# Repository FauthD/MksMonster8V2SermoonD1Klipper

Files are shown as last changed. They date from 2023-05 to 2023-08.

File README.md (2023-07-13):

# MksMonster8V2SermoonD1Klipper
Klipper settings for MKS Monster8 V2 build into the Creality Sermoon D1

This is WIP, do not use it yet.
I will add details here when it is ready and works.

# CAUTION: DO not use DFU with 24V connected with this board.
It can kill transistor Q7 (turning on bed heater all the time and Q7 gets very hot).
See there

[Bed is always heated after upgrade FW to v0.11.0-241-gffb5105b](https://github.com/makerbase-mks/MKS-Monster8/issues/40)

and

[V2 board starts burning when attempting dfu mode](https://github.com/makerbase-mks/MKS-Monster8/issues/26)

# Progress
[You can see many installation details there](InstallationJournal.md).

## Mechanics
Created an adapter to mount the Monster8 since it does not fit to the mounting holes. I also added some mounts for a big 120mm fan (because it was easier with a fan larger than the board). The fan runs with about 600 rmp and is barly audible.
There are also 3 mounting places for typical Step-Down regulators. I only use two for the fans, the third is spare.

Note: The monster board has 12V outputs for fans, so I would only need one step-down for the mainboard fan (7V), but the 12V step down was already wired from hystory (SKR 3 board). I am too lazy to change that right now.

| With 120mm fan |
| :----: |
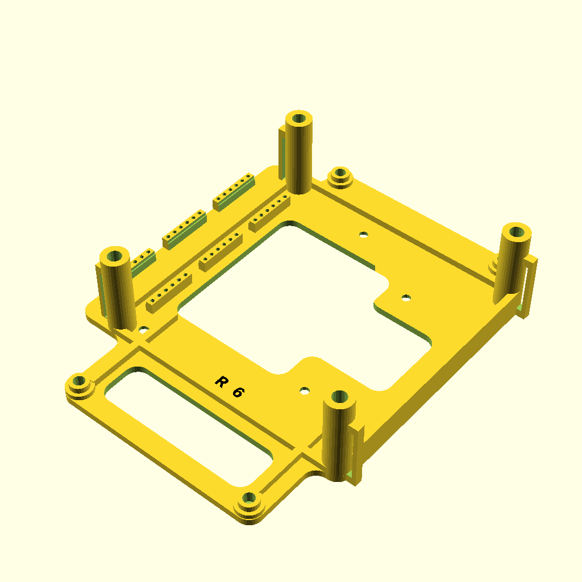
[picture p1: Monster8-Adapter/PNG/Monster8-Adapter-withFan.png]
|  

Note: You either need to cut a hole onto the bottom sheet or replace it with some new and larger feet (my plan).

Note2: The original mainboard fan does not transport much air, but makes quite some noise. So a slow turning 120mm fan is much better.
The next source of noise is the fan in the power supply. I replaced that fan with a low noise 120mm fan. Now it is barly audible.

Note3: We need heigher feet. Already printed some test feet with 28mm height (need 40mm screws - probably will increase by 5mm when I have that screws available).

Note4: I cannot check whether the original wires are long enough since I did buy the printer used and the wires are not original anymore.
## Klipper

Working on this.

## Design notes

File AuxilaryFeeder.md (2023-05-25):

# Auxilary feeder
## Rational
You might wonder why I do this? With my Sermoon D1 I often had issues with under extrution or the start of the print failed because the filament slipped out of the feeder. The first issue probably reulted ifrom the way I store the filament.

The extra feeder shall avoid transport problems.

## Hardware connection
The Monster 8 has 8 stepper drivers. For this auxilary feeder I use the driver5:E2.

This is the portion of the .cfg file. It is loctaed inside the extruder.cfg

```
[extruder_stepper auxilary_feeder]
extruder: extruder
# The extruder this stepper is synchronized to. If this is set to an
#  empty string then the stepper will not be synchronized to an
#  extruder. This parameter must be provided.
step_pin: PD2
dir_pin: PD1
enable_pin: !PD3
microsteps: 16
rotation_distance: 32.83
# See the "stepper" section for the definition of the above
# parameters.

[tmc2209 extruder_stepper auxilary_feeder]
uart_pin: PD0
run_current: 0.600
diag_pin:
```

## Testing low level
As with other steppers you can move the stepper back and forth with that command:

`STEPPER_BUZZ STEPPER="extruder_stepper auxilary_feeder"`

At my very first try it did not work, the enable pin needs the inverion flag: 
`enable_pin: !PD3`. After that the Stepper moved back and forth 10 times. (actually forth and back).

## Testing syncronization with extruder
Both the extruder (feeder) and the auxilary_feeder need to tranport the filament in sync. Therefor it should be sufficient to start extruding and the auxilary_feeder should transport the same ammount of filament. At this stage the amounts could still differ if the wheels have different diameters or the steps/mm are not the same.

So at least I want to see some transport.
1. Heat up the hotend to 200°C
2. Wait for heating up
3. Have filament in both the regular extruder and the auxilary one.
	I had used different filament pieces so they are independent from each other at this stage.
4. In the dashboard click on extrude.
5. Filamanets in both extruders should move in the same direction.
6. Same with retract.

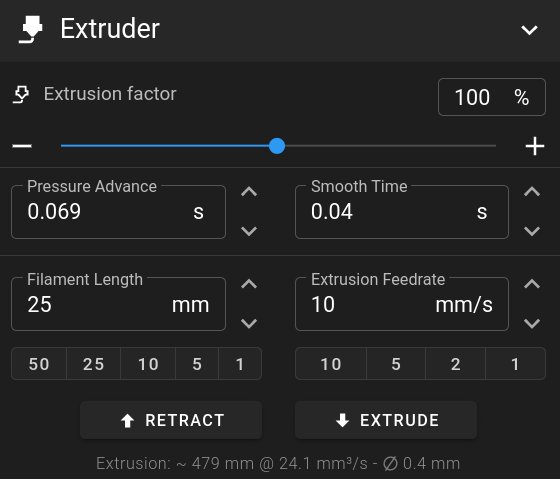
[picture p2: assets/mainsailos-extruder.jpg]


## Testing the amount of filament
Both extruders must transport the exact same amount of filament. For the test I use PLA from same manufacturer.

1. Mark the filamant in both feeders in same way as described in the Klipper docs (70mm).
	https://www.klipper3d.org/Rotation_Distance.html.
2. Set to relative coordinates `G91`.
3. Extrude 50mm with a slow speed `G1 E50 F60` to reduce the impact of filament melting.
4. Measure the (formerly) 70mm marks. They now should be 20mm away from the reference point.
	If not, calculate new rotation_distance values as described in the Klipper docs.
	In my case it was 20mm for both strings.
5. Do the same test with a higher speed `G1 E50 F600`.
	In my case there was quite a difference. Auxilary feeder was still at 20mm, but the normal feeder/extruder was at 35mm that means it only feeds 35mm instead 50mm.
	Currently I do not understand why the difference is that big.

# Reserching different filamant transport
Since the last test was not too pleasing, I tried the same with a heigher temperature (225 vs 200).
This time the normal extruder was at 32mm. A bit more filament was feed, but still way too less.

This could be a sign that my extruder has an issue. Or my expectations are plain wrong. Most likely the latter.

Increasing the current from 0.6A to 0.8A did not change much. I had hoped we loose steps, though normally this could be heared.

With `G1 E50 F200` the rest was 23mm which is still 3mm to less.

Visually I see the speed of the filament changes a bit while the test runs.
I will check the brass wheel of the extruder, but need to take it appart for this. What I can so so far it does not look too bad, but also not perfect. The allen screw sits absolut locked, need to take the complete head appart for better handling.

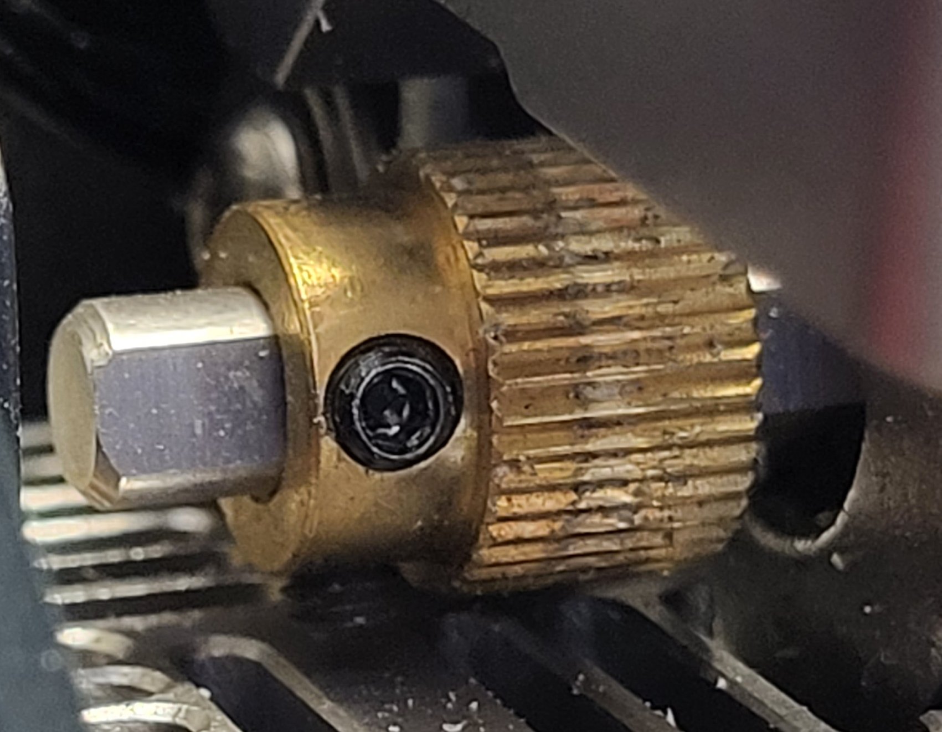
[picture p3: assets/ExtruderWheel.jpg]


With a new wheel it seems better, but at `G1 E50 F600` the extruder klicks. It is a sign that the old wheel was worn out.
Still a lot to do here. I guess it has nothing to do with the auxilary feeder, was just found randomly.

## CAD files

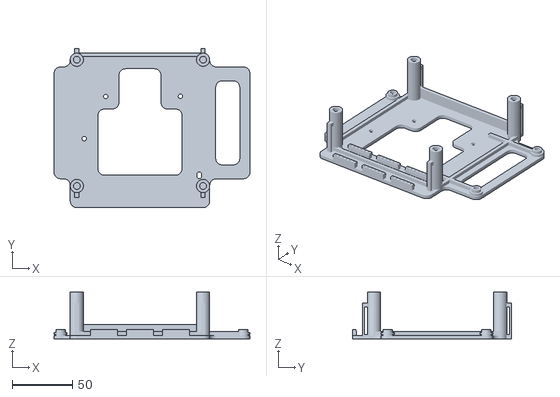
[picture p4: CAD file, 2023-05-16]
Monster8-Adapter/STL/Monster8-Adapter-withFan.stl
163.0 x 132.6 x 39.0

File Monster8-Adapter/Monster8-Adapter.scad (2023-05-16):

// An adapter to mount the MKS Monster 8 board into Creality mounting holes.
// Aimed for the Sermoon D1.
// For mounting you need 4 * M3 heat inserts (OD=5mm, l=4mm).
// I recommend to replace the original screws from the old board with ones with 
// flatter head.
// For the Fan you need 4 * M4 heat inserts (OD=6mm, l=5mm).
// Copyright (C) 2023 Dieter Fauth
// This program is free software: you can redistribute it and/or modify it under the terms of the GNU General Public License as published by the Free Software Foundation, either version 3 of the License, or (at your option) any later version.
// This program is distributed in the hope that it will be useful, but WITHOUT ANY WARRANTY; without even the implied warranty of MERCHANTABILITY or FITNESS FOR A PARTICULAR PURPOSE. See the GNU General Public License for more details. You should have received a copy of the GNU General Public License along with this program. If not, see <http://www.gnu.org/licenses/>.
// Contact: dieter.fauth at web.de

/* [Print] */

PrintThis = "all"; // ["all", "mount", "nothing"]

/* [Board Sizes] */
BoardLenght=160;
BoardWidth=90;

DrillLenght=152;
DrillWidth=82;
CrealityDrillDiameter=3.8;
// For M3 heat inserts use 4.5 else 2.5.
BoardDrillDiameter=4.7;
MountDiameter=8;
MountDiameter2=11;

MountHeight=6;
Thickness=3;

// Move Board to the left
Offset_X=-15;
// Move Board to upper
Offset_Y=10;

/* [Options] */
UseFan=true;
FanDiameter=120;
FanScrewDistance=105;
// For M4 heat inserts use 5.7 else 3.5.
FanScrewDiameters=5.7;
FanMountingPostDiameter=11;
FanHeight=36;
// Move Fan to the left
FanOffset_X=-10;

Fontsize=5;

/* [Hidden] */

module __Customizer_Limit__ () {}
    shown_by_customizer = false;

$fa = $preview ? 2 : 0.5;
$fs = $preview ? 1 : 0.5;

// If you enable the next line, the $fa and $fs are ignored.
// $fn = $preview ? 12 : 100;
Epsilon = 0.01;
epsilon = Epsilon;

include <svn_rev.scad>

/* Creality holes */
// These are relative to the lower left corner of the board.
// I took them from the BTT E3 Mini board.
// https://github.com/bigtreetech/BIGTREETECH-SKR-mini-E3/blob/master/hardware/BTT%20SKR%20MINI%20E3%20V3.0.1/Hardware/BTT%20E3%20SKR%20MINI%20V3.0.1_SIZE.pdf

E3Mini=[103.75, 70.25];

UnkownDifference=-1.0;  // one hole was not correct, empiric fix with a slotted hole

Drill1=[23.4,67.03, 0];
Drill2=[85.55, E3Mini.y-3.02, 0];
Drill3=[5.54, 32.05, 0];
Drill4=[37.34, 29.41, 0];
Drill5=[101.22, 2.56, 0];

Rounding=MountDiameter2/2;

FanOffset_Y=0;
Enlarge=3;

FanSize=FanScrewDistance+FanMountingPostDiameter;


///////////////////////////////////////////////////////////////////////////////
// halign: String. The horizontal alignment for the text. Possible values are "left", "center" and "right". Default is "left".
// valign : String. The vertical alignment for the text. Possible values are "top", "center", "baseline" and "bottom". Default is "baseline".

module WriteRevision(rev="", height=0.3, fontsize=6, font = "Liberation Mono:bold", halign="left", valign="top", mirror=false, rot=[0,0,0])
{
	rotate(rot)
		mirror([mirror?1:0,0,0])
			linear_extrude(height = height, center = true, convexity = 10)
			{
				text(rev, size=fontsize, font = font, halign=halign, valign=valign);
			}
}

///////////////////////////////////////////////////////////////////////////////
// Some helpers to round combined objects
module RoundConvex(r)
{
	offset(r = r)
	{
		offset(delta = -r)
		{
			children();
		}
	}
}

module RoundConcave(r)
{
	offset(r = -r)
	{
		offset(delta = r)
		{
			children();
		}
	}
}

module RoundThis(r)
{
	RoundConcave(r) RoundConvex(r) children();
}

// Can round combined 2D objects and make them 3D
module RoundExtrude(r, h)
{
	linear_extrude(height = h)
		RoundThis(r) children();
}

///////////////////////////////////////////////////////////////////////////////
// long hole
module SlottedHole(d, h, length)
{
   translate([0, 0, h/2])
      cube(size=[length, d, h+Epsilon], center=true);
      
   for(x=[-length/2,length/2])
   {
      translate([x, 0, h/2])
      {
         cylinder(d=d, h=h+Epsilon, center=true);
      }
   }
}

///////////////////////////////////////////////////////////////////////////////
// Helper for mounting step down boards with MP1584EN

module PcbMount(size, pcb)
{
   len=size.x;
   width=size.y+6;
   screw_dia=1.8;

   difference()
   {
      translate([0,0,size.z/2])
         cube([len,width, size.z], center=true);

      translate([0,0,size.z])
         cube([len+Epsilon,size.y, 2*pcb], center=true);

      translate([0,0,size.z/2])
         cube([len+Epsilon,size.y-1, size.z+Epsilon], center=true);

      for(n=[-1,1])
      {
         for(m=[-1:0.4:1])
         {
            translate([m*(len/2-2),n*(width/2-1.5),size.z/2])
               cylinder(d=screw_dia, h=20*size.z, center=true);
         }
      }
   }
}

MP1584EN_Size=[22.5, 17.1, 6.5];

module StepDown_MP1584EN()
{
   PcbMount(size=MP1584EN_Size, pcb=1.4);
}

///////////////////////////////////////////////////////////////////////////////
// The Fan

module Fan(h=25)
{
   for(a=[45:90:360-Epsilon])
   {
      rotate([0,0,a])
         translate([FanScrewDistance/1.414, 0, 0])
         {
            difference()
            {
               cylinder(d=FanMountingPostDiameter, h=h, center=true);
               translate([0,0,h/2])
                  cylinder(d=FanScrewDiameters, h=h, center=true);
            }
         }
   }
}
///////////////////////////////////////////////////////////////////////////////
// holder for cable tie
module CableMount(len=15, h=5)
{
	thick=3.5;
	translate([0,0,h/2])
		difference()
		{
			cube(size=[len, thick, h], center=true);

			translate([0,0,-thick/2])
				cube(size=[len-2*thick, 2*thick, h], center=true);
		}
}

///////////////////////////////////////////////////////////////////////////////
// The adapter

module CrealityHoles(d, h=5*Thickness)
{
   translate(Drill1)
      cylinder(d=d, h=h, center=true);
   translate(Drill2)
      cylinder(d=d, h=h, center=true);
   translate(Drill3)
      cylinder(d=d, h=h, center=true);
   translate(Drill4)
      cylinder(d=d, h=h, center=true);
   translate(Drill5)
      cylinder(d=d, h=h, center=true);
// fix some unknown difference in hole position
   translate([0,UnkownDifference,-h/2])
      translate(Drill5)
         rotate([0,0,90])
            SlottedHole(d=d, h=h, length=d/2);
}

module BoardHoles()
{
      for(x=[-1,1])
      {
         for(y=[-1,1])
         {
            translate([x*DrillLenght/2, y*DrillWidth/2, 0])
               cylinder(d=BoardDrillDiameter, h=10*Thickness);
         }
      }
}

module BasePlate()
{
   r=Rounding;

   RoundExtrude(r, Thickness)
   {
      square([BoardLenght+Enlarge, BoardWidth+Enlarge], center=true);
      // ensure the holes are covered by the size of the old board
      translate([Offset_X, -Offset_Y])
         square(E3Mini, center=true);


      x=E3Mini.x;
      y=E3Mini.y+7;
      translate([FanOffset_X, -12.5])
         square([FanSize, FanSize], center=true);

      if(UseFan)
      {
         translate([FanOffset_X, FanOffset_Y])
            square([FanSize, FanSize], center=true);
      }
   }
}

// also saves material
module CoolingHelper()
{
   RoundExtrude(Rounding, 10*Thickness)
   {
      translate([FanOffset_X+10, 15])
         square([35,60], center=true);

      translate([FanOffset_X+10, 25-DrillWidth/2])
         square([70,55], center=true);

      translate([BoardLenght/2-7, 0])
         square([20,70], center=true);
   }
}

module BoardMounts(l,w)
   {
      for(x=[-1,1])
      {
         for(y=[-1,1])
         {
            translate([x*l/2, y*w/2, MountHeight/2+Thickness])
               cylinder(d=MountDiameter, h=MountHeight, center=true);
            translate([x*l/2, y*w/2, MountHeight/2+Thickness-1])
               cylinder(d=MountDiameter2, h=MountHeight-3, center=true);
         }
      }
   }

module BoardHolder()
{
   BasePlate();
   BoardMounts(DrillLenght, DrillWidth);
}

module Adapter()
{
   difference()
   {
      union()
      {
         BoardHolder();
         extra=30;
         for(n=[1,0,-1])
         {
            translate([n*extra+FanOffset_X, -FanDiameter/2+1, Thickness/2])
               StepDown_MP1584EN();
         }
      }

      translate([0, 0, Thickness])
         BoardHoles();

      translate([-E3Mini.x/2+Offset_X, -E3Mini.y/2-Offset_Y, 0])
         CrealityHoles(CrealityDrillDiameter);

      dept=Thickness;
      translate([-E3Mini.x/2+Offset_X, -E3Mini.y/2-Offset_Y, 0])
         CrealityHoles(6.5,dept);
      
      // improve cooling
      translate([FanOffset_X,0,-Epsilon])
         CoolingHelper();
   }
   if(UseFan)
   {
      translate([FanOffset_X, FanOffset_Y, FanHeight/2+Thickness])
         Fan(h=FanHeight+Epsilon);
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

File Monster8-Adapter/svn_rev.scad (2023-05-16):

// Template file for SubWCRev

SVN_RevisionStr="R 6";

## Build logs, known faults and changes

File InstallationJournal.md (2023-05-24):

# Installation journal
This is WIP!

## Retrive information
```
gh repo clone makerbase-mks/MKS-Monster8
```
I am using V2.0 of the board. 

### Poor documentation from MKS
Unfortunatelly the documentation is quite poor, especially for the V2.0.
MKS should look into the docs of BTT (SKR3) to learn how a good documentation should look like.

- There is nothing that deserves the name manual.
- Schematics of the board cannot be searched through, it is pure graphics.
- No values are written in the schematics.
- Wire labels are not alligned correctly in many places (E.g. Reset at pin 14 of the MCU). This is just dirty.

## Preparation of the board

### Flash firmware
1. Copy "MKS-Monster8/klipper firmware/mks_monster8 v0.10.0-557.bin" to µSd-Card (FAT) as "firmware.bin".
2. Set jumper USBPWR to ON (behind the USB-C connector).
3. Plug µSd-Card into board.
4. Connect board to host (Linux PC or RPI). Wait 1 second. (24V supply is not needed)

On host open a terminal:
```
ls -l /dev/serial/by-id
```
Response:
```
total 0
drwxr-xr-x 2 root root 80 Mai 17 11:24 ./
drwxr-xr-x 4 root root 80 Mai 17 09:25 ../
lrwxrwxrwx 1 root root 13 Mai 17 11:24 usb-Klipper_stm32f407xx_39003E001250304B56333920-if00 -> ../../ttyACM0
```

Use this part: "/dev/serial/by-id/usb-Klipper_stm32f407xx_39003E001250304B56333920-if00"
for the mcu section.

Note: This device name contains the serial number of the board and is therefore different on each installation. Using this method avoids the volatile naming (ttyACM0).

```
[mcu]
serial: /dev/serial/by-id/usb-Klipper_stm32f407xx_39003E001250304B56333920-if00
```

5. Unplug the board.
6. Set jumper USBPWR back to OFF !

Big Note: As you can find more below, my very first attempt to flash the firmware did fail and I still had the MARLIN FW installed.
A second attempt was successful. So please check the name of the device to see whether it really contains KLIPPER.

### Set Jumpers

1. In my case I use TMC 2209 in UART mode:

    

2. Check the voltage for the fans. In my case I need 24V (VIN). These jumper are the factoy default.

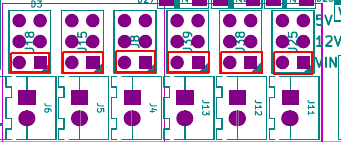
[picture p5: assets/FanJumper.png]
   

3. Check the jumper for end stop power. In my case I need 5V and this is the factory default.
	This is very important since I can probably fry the board?

   

4. Check the voltage for the TMC drivers. 5V is recommended and factory default.

   

5. Check Jumpers for heatings. These must be unpluged, or the heating will be off.
   This is J14, J16, J17, J19.

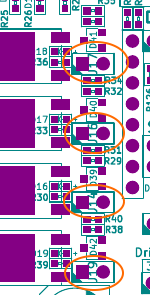
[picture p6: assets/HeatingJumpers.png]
   

6. There are more jumpers, for now I leave them at factory defaults. Perhaps I will come back later and add more details.

## Wiring
### Check polarity of connections
For luck I did not find any differences for the pinouts of the connectors. + and - are correct.
Only the BL_Touch will need extra care due to different connectors.

### CR Touch
Creatlity uses a 5 pin connector, SKR 3 uses a 3 pin + a 2 pin connector and the Monster 8 uses a 3 pin (without plasic protection) and a JST XH 3 pin connector.
So I had to unlock the two pins from the 2 pin JST and place then correctly into a 3 pin JST.
### Prepare Klipper config

Using the correct version of the PIN file. In my case it is located in "MKS-Monster8/hardware/MKS Monster8 V2.0_002/MKS Monster8 V2.0_002 PIN.pdf". You can also find the schematics in the same directory.

There is an example Klipper config "MKS-Monster8/klipper firmware/generic-mks-monster8.cfg".
In my case I had a working config for the BTT SKR3 board, so I used that as a starting point and adjusted the pin definitions to the monster 8.

Both the example config (copy paste some lines) and the PIN definition file (PDF named above) do help with details. Below is a screenshot of the pin definitions to ensure you find the right file.

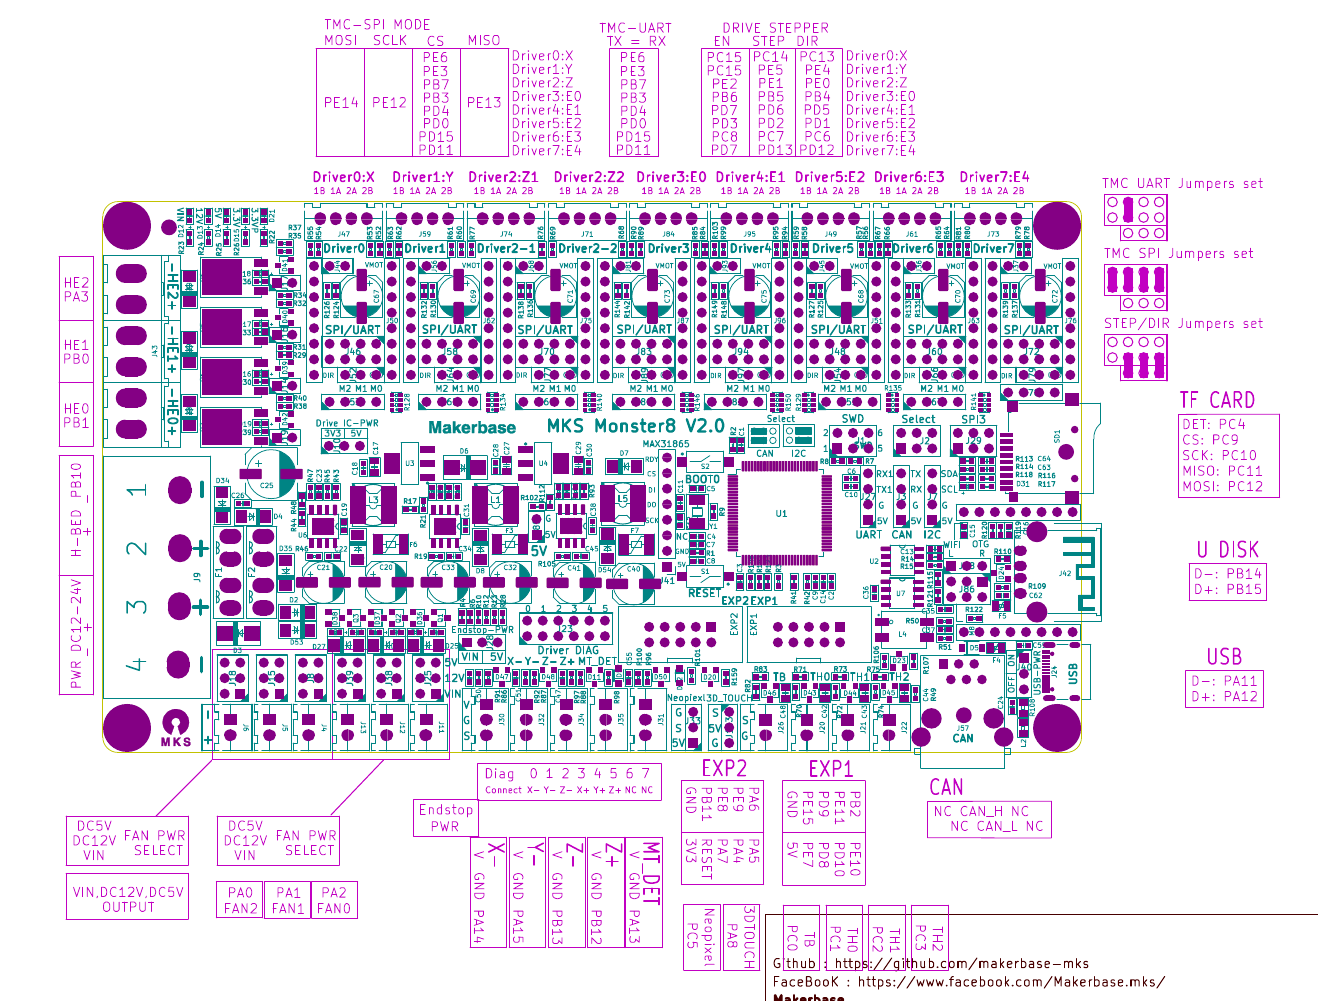
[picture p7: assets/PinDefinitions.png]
   

Klipper supports the split the config into several files. This help to find the right stuff later. Therefore my printer.cfg mostly contains include statements.

printer.cfg
```
[include mainsail.cfg]
[include sermoon_d1.cfg]
[include stepper.cfg]
[include extruder.cfg]
[include bed_screws.cfg]
[include bltouch.cfg]
[include z_tilt.cfg]
[include heater_bed.cfg]
[include fans.cfg]
[include mcu.cfg]
[include display.cfg]
[include filament_sensor.cfg]
[include leds.cfg]
[include input_shaper.cfg]
[include macros/macros.cfg]

# bltouch must be directly in printer.cfg in order the SAVE_CONFIG can work
[bltouch]
....

```

## Initial start up
Klipper does not find the MCU.

```
mcu 'mcu': Timeout on connect
mcu 'mcu': Wait for identify_response
Traceback (most recent call last):
  File "/home/pi/klipper/klippy/serialhdl.py", line 68, in _get_identify_data
    params = self.send_with_response(msg, 'identify_response')
  File "/home/pi/klipper/klippy/serialhdl.py", line 261, in send_with_response
    return src.get_response([cmd], self.default_cmd_queue)
  File "/home/pi/klipper/klippy/serialhdl.py", line 318, in get_response
    self.serial.raw_send_wait_ack(cmds[-1], minclock, reqclock,
  File "/home/pi/klipper/klippy/serialhdl.py", line 253, in raw_send_wait_ack
    self._error("Serial connection closed")
  File "/home/pi/klipper/klippy/serialhdl.py", line 61, in _error
    raise error(self.warn_prefix + (msg % params))
serialhdl.error: mcu 'mcu': Serial connection closed
```
Double checked the symlink and even tried /dev/ttyACM0.
Checked whether the modem manager is istalled and uninstalled it since it grabs the 
serial line for the first ~20 secs after a plug-in event (for CDC ACM devices). A udev rule can prevent the MM from touching the device, 
but removing it is easier for now.
```
sudo apt remove modemmanager
```
No success yet.

Well, it seams my initial attempt to write the klipper firmware did not work. After re-reading the symlink a few dozend times I saw it contained MARLIN. Sure it does not work.
```
/dev/serial/by-id/usb-STMicroelectronics_MARLIN_STM32F407VGT6_CCM_CDC_in_FS_Mode_2077338F4B30-if00
```
Did the firmware flash procedure again, and indeed the file was renamed to FIRMWARE.CUR. And the symlink now contains KLIPPER.
```
/dev/serial/by-id/usb-Klipper_stm32f407xx_39003E001250304B56333920-if00
```

Now Klipper connects to the MCU and I can proceed with further tests. I follow the guide there:
 https://www.klipper3d.org/Config_checks.html.

# Klipper Configuration checks
Though I do not use octoprint, this guide is very help full even with Mainsail.
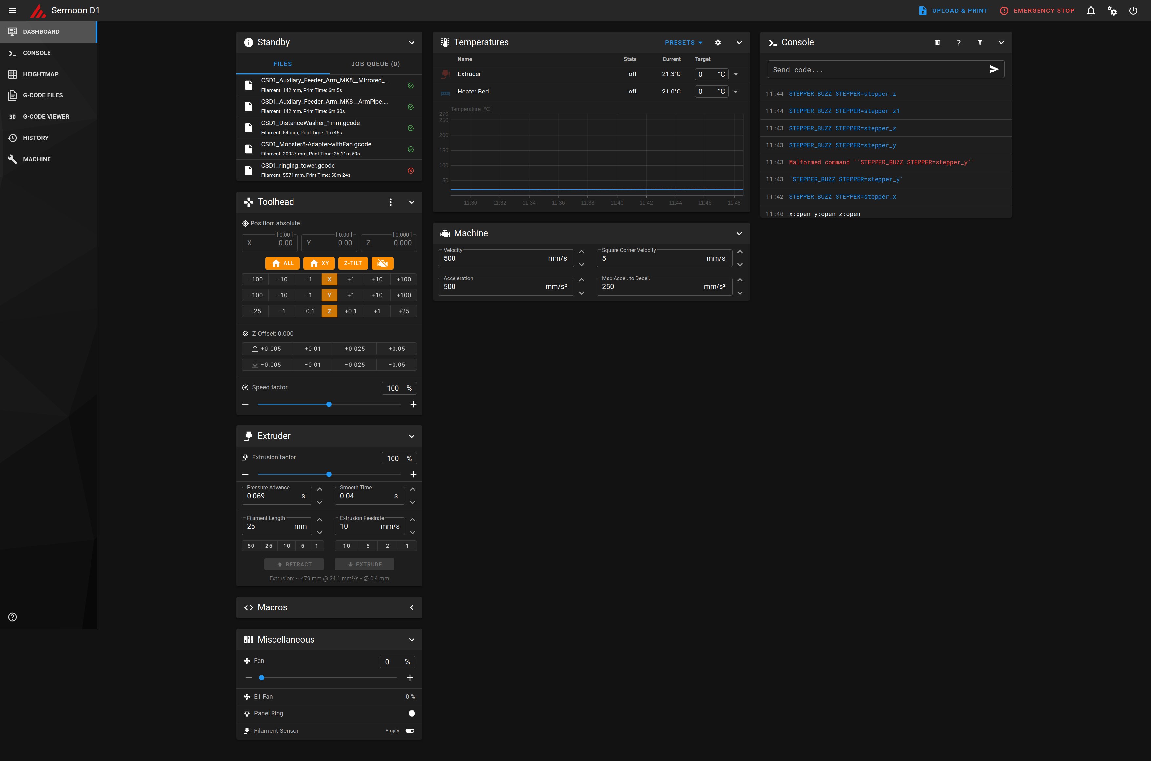
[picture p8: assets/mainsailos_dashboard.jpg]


## Checking the heatings
In webinterface (Mainsail in my case), set set a bed temperature of 30°C, check whether temperature goes to 30°C and stays there.
Same with hot end. Check whether the fan in the hotend runs.
All passed in my case.

### PID Tuning for bed
This can take quite some time for a thick bed (mine is 9mm thick).
This command does start the PID tuning:
`PID_CALIBRATE HEATER=heater_bed TARGET=60`

Take the pid_xxx values from the response and add to the heater_bed section. Ensure you replace the '=' with ':'.
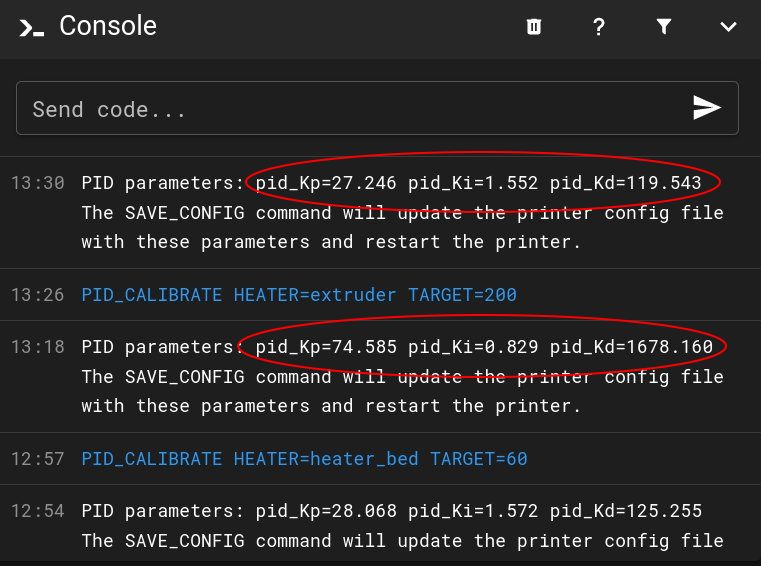
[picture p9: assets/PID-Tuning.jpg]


My heater_bed.cfg
```
[heater_bed]
heater_pin: PB10
sensor_type: EPCOS 100K B57560G104F
sensor_pin: PC0
control: pid
# after PID_CALIBRATE HEATER=heater_bed TARGET=60
pid_Kp:74.585
pid_Ki:0.829
pid_Kd:1678.160
min_temp: 0
max_temp: 100
```
### PID Tuning for hotend
This command does start the PID tuning:
`PID_CALIBRATE HEATER=extruder TARGET=200`

Klipper rises and lowers temperature to measure the parameters of the "controlled section" to
finally calculate the closed loop paramters (I assume per Ziegler-Nichols).

Take the pid_xxx values from the response and add to the extruder section. Ensure you replace the '=' with ':'.

My extruder.cfg
```
[extruder]
max_extrude_only_distance: 1000.0
step_pin: PB5
dir_pin: !PB4
enable_pin: !PB6
microsteps: 16
# after calibration
rotation_distance: 32.83
#rotation_distance: 33.500
nozzle_diameter: 0.400
filament_diameter: 1.750
heater_pin: PB1
sensor_type: EPCOS 100K B57560G104F
sensor_pin: PC1
control: pid
# after PID_CALIBRATE HEATER=extruder TARGET=200
pid_Kp:27.246
pid_Ki:1.552
pid_Kd:119.543
min_temp: 0
max_temp: 260

[tmc2209 extruder]
uart_pin: PB3
run_current: 0.600
diag_pin:
```

## Verify stepper motor enable pin
All motors can be moved easily. Well, except the extruder which I cannot test right now.

## Verify endstops
Since I use a CR Touch, there are only X and Y endstops. Let them check.
Command `QUERY_ENDSTOPS`  responds with
```
x:TRIGGERED y:TRIGGERED z:open
```
That is wrong, need to invert the inputs (remove the ! in front of the pin definition) and restart Klipper.
Now it is correct.
```
x:open y:open z:open
```
Now, do they actually trigger? Move both the X and Y axis to the zero point and reissue `QUERY_ENDSTOPS`.
```
x:TRIGGERED y:TRIGGERED z:open
```
Well done, endstops work.

## Steppers
Move back both X and Y to about the center. The `STEPPER_BUZZ` command moves an axis 10 times forth and back (1mm).
```
STEPPER_BUZZ STEPPER=stepper_x
STEPPER_BUZZ STEPPER=stepper_y
STEPPER_BUZZ STEPPER=stepper_z
STEPPER_BUZZ STEPPER=stepper_z1
```

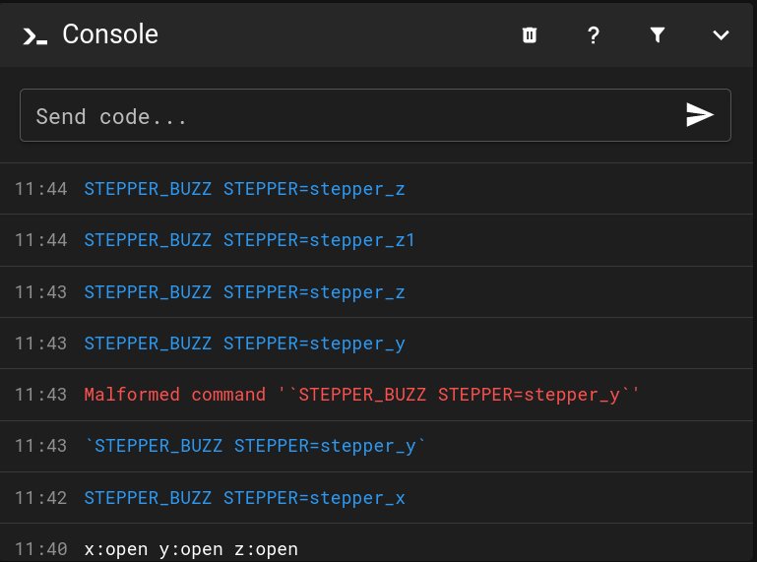
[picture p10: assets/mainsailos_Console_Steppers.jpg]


BTW: Cursor up brings the last command back, so it can be reissued or edited.

The test result showed that the X and Z axis are running backwards. Only Y and Z1 seems to be correct. And indeed, some of the dir_pin setting had no '!'. Only the correct ones had the '!'. Adding the '!' to all of the dir_pin setups and restart Klipper.

Now all axes but the Y look correct. Double check my old SKR 3 config. Even there the Y axis was different from the other axes. Most likley the wiring for the Y-Stepper is the root cause (it was not origial as I did buy the printer).

**In case you use my config as a starting point, check carefully here all the axes.**

In my case it looks good now.

## Homing test for X and Y
The dashboard offers buttons to start the homming for each of the axes.

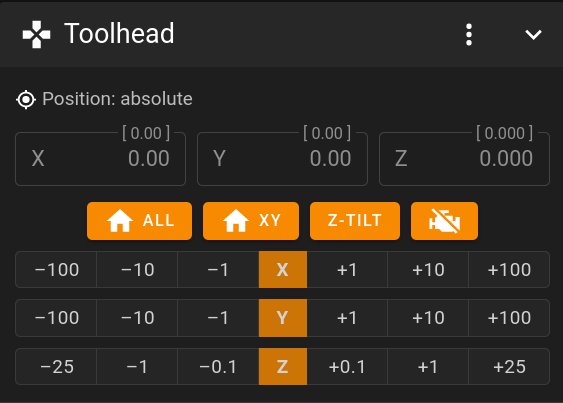
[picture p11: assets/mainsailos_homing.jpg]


Both the X and Y do home properly. Now I need to check the CR Touch to be able to home the Z axis.

My stepper.cfg
```
# Note: X and Y do use the same enable pin.

[stepper_x]
step_pin: PC14
dir_pin: !PC13
enable_pin: !PC15
microsteps: 64
rotation_distance: 40
endstop_pin: PA14
position_min: -5
position_endstop: -5
position_max: 280
homing_speed: 50

[stepper_y]
step_pin: PE5
dir_pin: PE4
enable_pin: !PC15
microsteps: 64
rotation_distance: 40
endstop_pin: PA15
position_min: -5
position_endstop: -5
position_max: 260
homing_speed: 50

[stepper_z]
step_pin: PE1
dir_pin: PE0
enable_pin: !PE2
microsteps: 64
rotation_distance: 8
endstop_pin: probe:z_virtual_endstop
#endstop_pin: !PB13
#position_endstop: 0.5
position_max: 300
homing_speed: 4
second_homing_speed: 1
homing_retract_dist: 2.0
position_min: -1

# This is marked as E1 stepper driver on Monster 8
[stepper_z1]
step_pin: PD6
dir_pin: PD5
enable_pin: !PD7
microsteps: 64
rotation_distance: 8
endstop_pin: probe:z_virtual_endstop

########################################
# TMC2209 configuration
########################################

[tmc2209 stepper_x]
uart_pin: PE6
run_current: 0.800
diag_pin:
#stealthchop_threshold: 0
stealthchop_threshold: 999999

[tmc2209 stepper_y]
uart_pin: PE3
run_current: 0.800
diag_pin:
#stealthchop_threshold: 0
stealthchop_threshold: 999999

[tmc2209 stepper_z]
uart_pin: PB7
run_current: 0.8
diag_pin:
interpolate: False
#stealthchop_threshold: 0
stealthchop_threshold: 999999

[tmc2209 stepper_z1]
uart_pin: PD4
run_current: 0.8
diag_pin:
interpolate: False
#stealthchop_threshold: 0
stealthchop_threshold: 999999
```

### CR Touch
https://www.klipper3d.org/BLTouch.html

Pin down: `BLTOUCH_DEBUG COMMAND=pin_down` - works.

Pin up: `BLTOUCH_DEBUG COMMAND=pin_up` - works.

Does it trigger?
1. Again: `BLTOUCH_DEBUG COMMAND=pin_down`
2. `BLTOUCH_DEBUG COMMAND=touch_mode`
3. `QUERY_PROBE` - "probe: open"
4. Gently push it up
5. `QUERY_PROBE` - "probe: triggered"
6. `BLTOUCH_DEBUG COMMAND=pin_up`

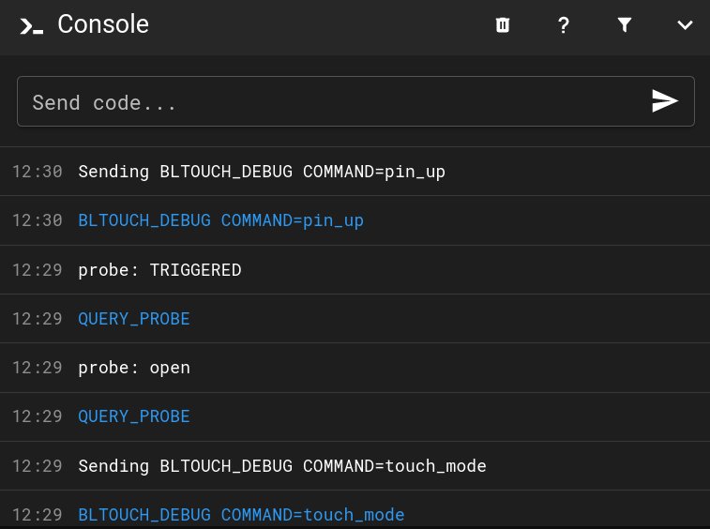
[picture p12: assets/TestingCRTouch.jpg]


Ok, now lets home the Z axis. Watch carefully that both axes move correclty. **Know how to abort in error case.**

Works just fine here.

My bltouch.cfg
```
 Before printing the PROBE_CALIBRATE command needs to be issued
# to run the probe calibration procedure, described at
# docs/Probe_Calibrate.md, to find the correct z_offset.

[safe_z_home]                           # enable for BLTouch
home_xy_position: 93, 143
speed: 100
z_hop: 10
z_hop_speed: 5

# bltouch must be directly in printer.cfg in order the SAVE_CONFIG can work

[bed_mesh]                              # enable for BLTouch
speed: 100
mesh_min: 50, 5
mesh_max: 270, 250
algorithm: bicubic
probe_count: 10, 10
fade_start: 1
fade_end: 10
fade_target: 0
```
Since some portions need to be located directly in the printer.cfg:
```
# bltouch must be directly in printer.cfg in order the SAVE_CONFIG can work
[bltouch]
sensor_pin: ^PB13
control_pin: PA8
x_offset: 49
y_offset: -6
#z_offset: 1.656
speed: 3.0
```

### Z Tilt
Since I had z-tilt working already with ym SKR 3, I expect with works the same. Pressing the Z-Tilt button start it. Or enter Z-Tilt in the console.

Works just fine here.

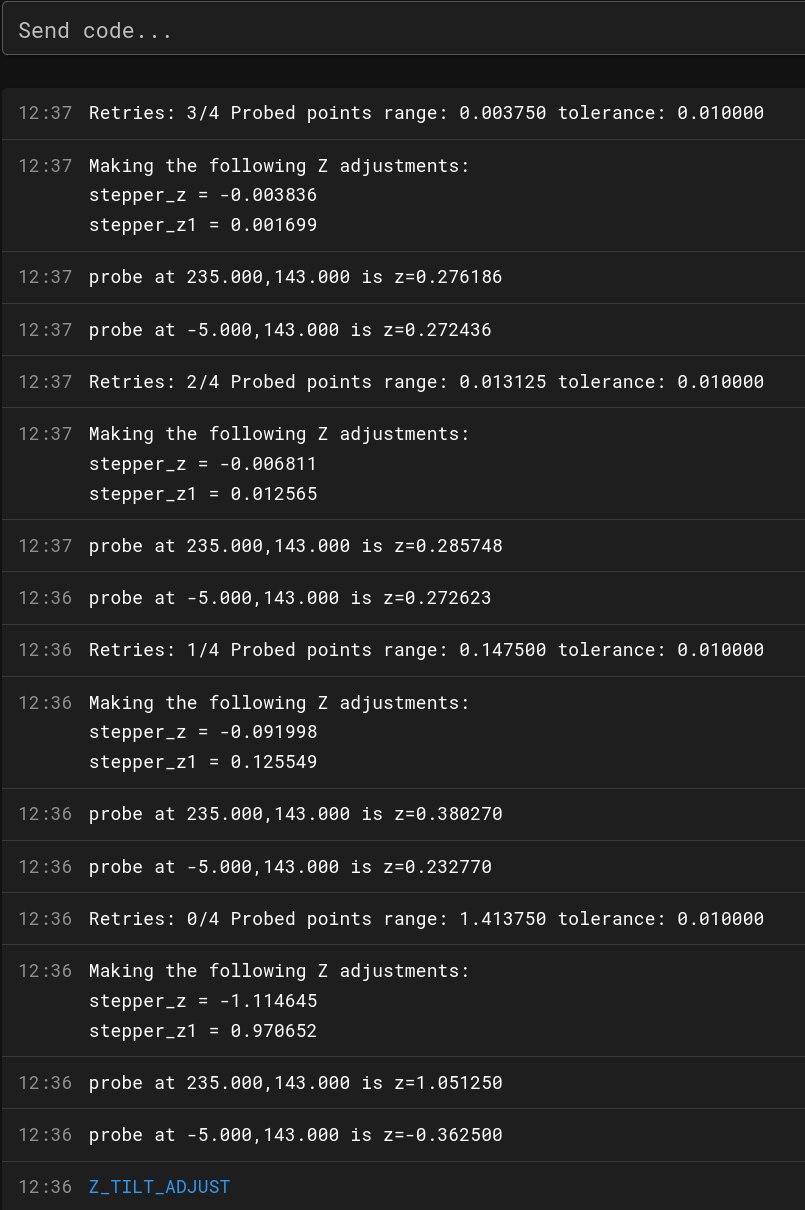
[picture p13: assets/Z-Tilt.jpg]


My Z-Tilt configuration might not fit to your printer, it depends on where the CR-Touch is mounted.

File z-tilt.cfg:
```
[z_tilt]
z_positions:
  -37,137
  317,137
#   A list of X, Y coordinates (one per line; subsequent lines
#   indented) describing the location of each bed "pivot point". The
#   "pivot point" is the point where the bed attaches to the given Z
#   stepper. It is described using nozzle coordinates (the X, Y position
#   of the nozzle if it could move directly above the point). The
#   first entry corresponds to stepper_z, the second to stepper_z1,
#   the third to stepper_z2, etc. This parameter must be provided.

points:
  -5,143
  235,143
#  197,143
#   A list of X, Y coordinates (one per line; subsequent lines
#   indented) that should be probed during a Z_TILT_ADJUST command.
#   Specify coordinates of the nozzle and be sure the probe is above
#   the bed at the given nozzle coordinates. This parameter must be
#   provided.

#speed: 50
#   The speed (in mm/s) of non-probing moves during the calibration.
#   The default is 50.
#horizontal_move_z: 5
#   The height (in mm) that the head should be commanded to move to
#   just prior to starting a probe operation. The default is 5.

retries: 4
#   Number of times to retry if the probed points aren't within
#   tolerance.

retry_tolerance: 0.01
#   If retries are enabled then retry if largest and smallest probed
#   points differ more than retry_tolerance. Note the smallest unit of
#   change here would be a single step. However if you are probing
#   more points than steppers then you will likely have a fixed
#   minimum value for the range of probed points which you can learn
#   by observing command output.
```

### Testing the filament runout sensor
On lower part of the dashboard there is the runout sensor. Check that the staus is correct in both cases.
If it shows "disabled", then click on it to enable.




filament_sensor.cfg
```
[filament_switch_sensor filament_sensor]
pause_on_runout: true
switch_pin: !PA13
```
### Extruder
Now that heatings are working and the other axes, the extruder is the last one to get tested.
1. Set temperatur to 205°C
2. wait until it is hot
3. With some filament inserted (was from last print), click "retract" in the dashboard.
   In my case it actually extruded. That means the direction is wrong and I had to 
   remove the '!' from the step_dir setting of the extruder. Restart Klipper to use the new settings.
   After such a change, start with 1.
   If retract and extrude work with the correct direction, you might want to calibrate the "steps".
   In my case this was already done earlier and a board swap should not change these values.



extruder.cfg as it now looks like.
```
[extruder]
max_extrude_only_distance: 1000.0
step_pin: PB5
dir_pin: PB4
enable_pin: !PB6
microsteps: 16
# after calibration
rotation_distance: 32.83
#rotation_distance: 33.500
nozzle_diameter: 0.400
filament_diameter: 1.750
heater_pin: PB1
sensor_type: EPCOS 100K B57560G104F
sensor_pin: PC1
control: pid
# after PID_CALIBRATE HEATER=extruder TARGET=200
pid_Kp:27.246
pid_Ki:1.552
pid_Kd:119.543
min_temp: 0
max_temp: 260
pressure_advance: 0.069

[tmc2209 extruder]
uart_pin: PB3
run_current: 0.600
diag_pin:
```

[See my setup of an auxilary feeder there](AuxilaryFeeder.md).

### LEDs
The LED strip just arrived 5 minutes ago, so I test it right away. It is a SK6812 RGBW strip and different from the 
one I used to test this with the SKR 3. https://de.aliexpress.com/item/4000907649687.html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

It has 5 wires connected to it. What are the two extra wires for? Ok, the two extra wires are for extra 5V and GND. For now I leave them unconnected.
The connector fits to the 3 pins of the Monster 8. - Working.

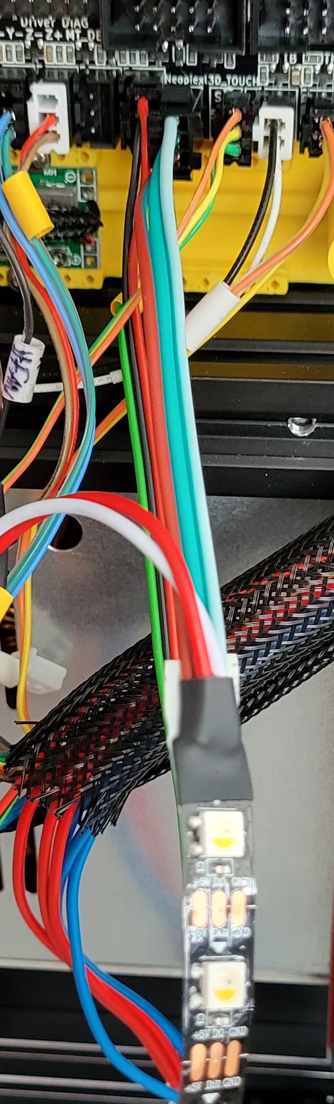
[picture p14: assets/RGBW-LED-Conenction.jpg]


```
[neopixel panel_ring]
pin: PC5
#   The pin connected to the neopixel. This parameter must be
#   provided.
chain_count: 60
#   The number of Neopixel chips that are "daisy chained" to the
#   provided pin. The default is 1 (which indicates only a single
#   Neopixel is connected to the pin).
color_order: GRBW
#   Set the pixel order required by the LED hardware (using a string
#   containing the letters R, G, B, W with W optional). Alternatively,
#   this may be a comma separated list of pixel orders - one for each
#   LED in the chain. The default is GRB.
initial_RED: 1.0
initial_GREEN: 1.0
initial_BLUE: 1.0
initial_WHITE: 1.0
#   See the
```

To be continued....perhaps :-)

```

```
```

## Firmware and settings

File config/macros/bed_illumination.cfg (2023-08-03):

# internal macros
[gcode_macro _BED_DARK]
gcode:
	SET_LED LED=left_bed_illumination RED=0.0 GREEN=0.0 BLUE=0.0 WHITE=0.0

[gcode_macro _BED_WHITE]
gcode:
	SET_LED LED=left_bed_illumination RED=1.0 GREEN=0.6 BLUE=0.5 WHITE=1.0

[gcode_macro _BED_RED]
gcode:
	SET_LED LED=left_bed_illumination RED=1.0 GREEN=0.0 BLUE=0.0 WHITE=0.0

[gcode_macro _BED_DARKRED]
gcode:
	SET_LED LED=left_bed_illumination RED=0.1 GREEN=0.0 BLUE=0.0 WHITE=0.0

[gcode_macro _BED_GREEN]
gcode:
	SET_LED LED=left_bed_illumination RED=0.0 GREEN=1.0 BLUE=0.0 WHITE=0.0

[gcode_macro _BED_BLUE]
gcode:
	SET_LED LED=left_bed_illumination RED=0.0 GREEN=0.0 BLUE=1.0 WHITE=0.0

[gcode_macro _BED_MAGENTA]
gcode:
	SET_LED LED=left_bed_illumination RED=1.0 GREEN=0.0 BLUE=0.05 WHITE=0.0

[gcode_macro _BED_YELLOW]
gcode:
	SET_LED LED=left_bed_illumination RED=1.0 GREEN=0.4 BLUE=0.0 WHITE=0.2

[gcode_macro _BED_DARKYELLOW]
gcode:
	SET_LED LED=left_bed_illumination RED=0.5 GREEN=0.1 BLUE=0.0 WHITE=0.0

# Use these from other places
[gcode_macro _BED_ILLUMINATION_START]
gcode:
	_BED_DARKRED
	
[gcode_macro _BED_ILLUMINATION_HOME]
gcode:
	_BED_RED

[gcode_macro _BED_ILLUMINATION_TILT]
gcode:
	_BED_MAGENTA

[gcode_macro _BED_ILLUMINATION_WAIT]
gcode:
	_BED_DARKYELLOW

[gcode_macro _BED_ILLUMINATION_PRIME]
gcode:
	_BED_YELLOW

[gcode_macro _BED_ILLUMINATION_PRINT]
gcode:
	_BED_WHITE

[gcode_macro _BED_ILLUMINATION_FINISHED]
gcode:
	_BED_GREEN

[gcode_macro _BED_ILLUMINATION_STOP]
gcode:
	_BED_DARK

##########################################################

[gcode_macro _BED_ILLUMINATION_LOADSTART]
gcode:
	_BED_DARKYELLOW
	
[gcode_macro _BED_ILLUMINATION_LOAD1]
gcode:
	_BED_RED

[gcode_macro _BED_ILLUMINATION_LOAD2]
gcode:
	_BED_MAGENTA

[gcode_macro _BED_ILLUMINATION_LOAD3]
gcode:
	_BED_BLUE

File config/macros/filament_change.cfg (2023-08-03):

######################################################################
# Filament Change
######################################################################

# M600: Filament Change. This macro will pause the printer, move the
# tool to the change position, and retract the filament 50mm. Adjust
# the retraction settings for your own extruder. After filament has
# been changed, the print can be resumed from its previous position
# with the "RESUME" gcode.

# This is construction zone!!!!!!

[pause_resume]

# [gcode_macro M600]
# gcode:
#     {% set X = params.X|default(50)|float %}
#     {% set Y = params.Y|default(0)|float %}
#     {% set Z = params.Z|default(10)|float %}
#     SAVE_GCODE_STATE NAME=M600_state
#     PAUSE
#     G91
#     G1 E-.8 F2700
#     G1 Z{Z}
#     G90
#     G1 X{X} Y{Y} F3000
#     G91
#     G1 E-50 F1000
#     RESTORE_GCODE_STATE NAME=M600_state

###########################################################
# MOVE_AUXILARY_FEEDER DISTANCE=50 VELOCITY=100
[gcode_macro MOVE_AUXILARY_FEEDER]
gcode:
    {% set Distance = params.DISTANCE|default(60)|float %}
    {% set Velocity = params.VELOCITY|default(30)|float %}
    FORCE_MOVE STEPPER="extruder_stepper auxilary_feeder" DISTANCE={Distance} VELOCITY={Velocity}


###########################################################
[gcode_macro LOAD_FILAMENT]
gcode:
    {% set speed = params.SPEED|default(300) %}
    {% set distance = params.DISTANCE|default(670) %}
    {% set max_velocity = printer.configfile.settings['extruder'].max_extrude_only_velocity %}
    SAVE_GCODE_STATE NAME=load_state
    # M300 # beep
    _BED_ILLUMINATION_LOADSTART
    MOVE_AUXILARY_FEEDER DISTANCE=20 VELOCITY=30
    _BED_ILLUMINATION_LOAD1
    MOVE_AUXILARY_FEEDER DISTANCE={distance} VELOCITY=80
    _BED_ILLUMINATION_LOAD2
    #G91
    G92 E0     ; Reset the extruder's origin
    #G1 E30 F{max_velocity} # fast-load
    G1 E60 F1000
    _BED_ILLUMINATION_LOAD3
    #G1 E140 F{speed} # purge
    G1 E100 F500 # purge
    # M300
    # M300
    _BED_ILLUMINATION_STOP
    RESTORE_GCODE_STATE NAME=load_state

[gcode_macro UNLOAD_FILAMENT]
gcode:
    {% set speed = params.SPEED|default(300) %}
    {% set distance = params.DISTANCE|default(720) %}
    {% set max_velocity = printer.configfile.settings['extruder'].max_extrude_only_velocity %}
    SAVE_GCODE_STATE NAME=unload_state
    #G91
    # M300 # beep
    _BED_ILLUMINATION_LOADSTART
    G92 E0     ; Reset the extruder's origin
    G1 E15 F{speed} # purge
    _BED_ILLUMINATION_LOAD1
#    G1 E-80 F{max_velocity} # fast-unload
    G1 E-80 F500 # fast-unload
    _BED_ILLUMINATION_LOAD2
    #MOVE_AUXILARY_FEEDER DISTANCE=-20 VELOCITY=30
    #_BED_ILLUMINATION_LOAD3
    MOVE_AUXILARY_FEEDER DISTANCE=-{distance} VELOCITY=100
    # M300
    # M300
    _BED_ILLUMINATION_STOP
    RESTORE_GCODE_STATE NAME=unload_state

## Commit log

2023-05-01 Adding config based on my SKR3 files.
    [bed_screws.cfg, beeper.cfg, bltouch.cfg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]
2023-05-01 Change to port pins of the Moster 8.
    [display.cfg, extruder.cfg, fans.cfg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]
2023-05-16 Add mounting adapter and minor adds to readme.
    [Monster8-Adapter-withFan.stl, Monster8-Adapter.scad, svn_rev.scad]
2023-05-16 Add the original klipper example config from Mks fir reference.
    [generic-mks-monster8.cfg]
2023-05-24 Sync my working config from Klipper.
    [bltouch.cfg, extruder.cfg, fans.cfg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]
2023-05-25 Increase current for extruder stepper.
    [extruder.cfg]
2023-05-25 A first try for input shaping.
    [input_shaper.cfg]
2023-05-25 Add illumination.
    [bed_illumination.cfg, leds.cfg, macros.cfg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]
2023-06-06 z tilt now uses symetric probe points in the hope to reduce retries.
    [z_tilt.cfg]
2023-06-06 Adjust auxilary extruder to new way of mount (mirrored). Increase motor current 10 1A, aux reduxce to 0.5A.
    [extruder.cfg]
2023-06-06 Remove double sending of led colors, it does not help.
    [bed_illumination.cfg]
2023-06-06 Optimize START_PRINT macro.
    [start_end.cfg]
2023-06-06 Add firmware retraction.
    [printer.cfg, retraction.cfg]
2023-07-13 Add global variables for mainsail.
    [printer.cfg, variables.cfg]
2023-07-13 Increase speed of z tilt.
    [z_tilt.cfg]
2023-07-31 Increase current fir auxilary_feeder. Prepare for a filement load/unload macro with the auxilary_feeder alone.
    [extruder.cfg]
2023-07-31 Optimize start end macros.
    [start_end.cfg]
2023-07-31 Adjust led colors a bit.
    [bed_illumination.cfg]
2023-08-03 Teak bedsizes. The bed is 10mm bigger than specified. Could be 5 more, but some screw are in the way.
    [bltouch.cfg, stepper.cfg, variables.cfg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]
2023-08-03 Add an extra neopixel led that acts as a levelshifter (its vcc is lowered by a diode: 1n4148). Now the colors are correct.
    [leds.cfg]
2023-08-03 Add a commented out extra mcu for experiments.
    [mcu.cfg]
2023-08-03 Store the med mesch after tweaking the sizes.
    [printer.cfg]
2023-08-03 Move the parking position a bit to the inside of the bed.
    [start_end.cfg]
2023-08-03 Add a first test for the change filament macros that also uses the auxiilary extruder. This will need more tweaks.
    [bed_illumination.cfg, filament_change.cfg]
